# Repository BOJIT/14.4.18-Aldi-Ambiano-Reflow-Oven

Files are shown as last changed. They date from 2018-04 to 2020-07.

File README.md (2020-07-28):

# Aldi Ambiano Reflow Oven
Dirt cheap, easily replicable SMD reflow oven based on an Arduino Nano
and the £19.99 Aldi Ambiano Mini Oven

Developers: James Bennion-Pedley

Firmware closely based on work by https://github.com/giacu92/Arduino-Reflow-Oven-Controller

Project Write-Up Here: [https://bojit.dev/projects/Reflow_Oven/]

BOJIT Development Team

GPLv3 License

Copyright (c) 2018 BOJIT

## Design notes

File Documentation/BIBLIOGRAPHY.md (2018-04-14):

# Aldi Ambiano Reflow Oven
Dirt cheap, easily replicable SMD reflow oven based on an Arduino Nano
and the £19.99 Aldi Ambiano Mini Oven

Developers: James Bennion-Pedley

BOJIT Development Team

Sources and Links:

https://github.com/giacu92/Arduino-Reflow-Oven-Controller
https://github.com/0xPIT/reflowOvenController

MIT License

Copyright (c) 2018 BOJIT

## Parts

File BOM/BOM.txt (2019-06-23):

Ceramic Insulation	£14.00	https://www.ebay.co.uk/itm/CERAMIC-INSULATION-BLANKET-WOOD-BURNING-PIZZA-OVEN-FURNACE-WOOL-25mm-HIGH-TEMP/323415218165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
High-Temperature Wire	£1.79	https://www.ebay.co.uk/itm/High-Temperature-Oven-Heat-Fire-Resistant-Braided-Glass-Fibre-Wire-cable-2-5mm/112352955954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
Silicon Sealant		£2.79	https://www.ebay.co.uk/itm/BLACK-HIGH-TEMPERATURE-300-C-SILICONE-Heat-Resistant-ADHESIVE-SEALANT-Technicqll-/291793420033
2 x SSR			£6.34	https://www.ebay.co.uk/itm/2PCS-Solid-State-Relay-SSR-25DA-25A-250V-3-32V-DC-Input-24-380VAC-Output-NEW/141676282282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
Thermocouple + Breakout	£2.82	https://www.ebay.co.uk/itm/MAX6675-Module-K-Type-Thermocouple-Temperature-Sensor-For-Arduino-UK/153327741272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
16x2 LCD		£3.24	https://www.ebay.co.uk/itm/1602-16x2-LCD-Display-Module-BLUE-white-character-Serial-Arduino-Raspberry-PI/292453360759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

Total			£30.98

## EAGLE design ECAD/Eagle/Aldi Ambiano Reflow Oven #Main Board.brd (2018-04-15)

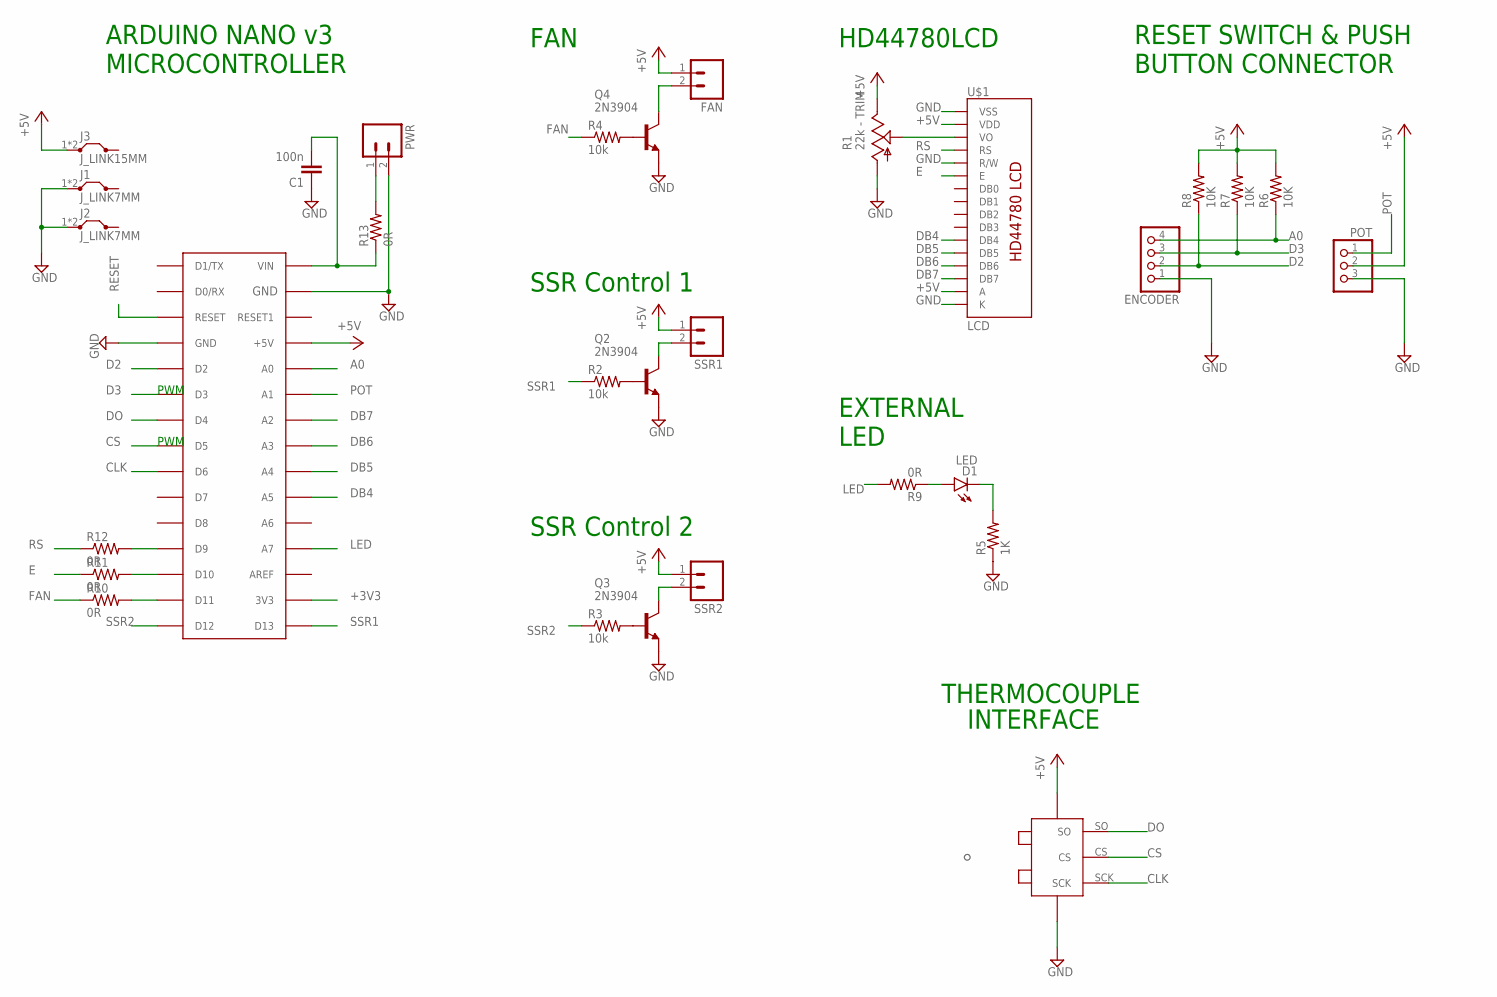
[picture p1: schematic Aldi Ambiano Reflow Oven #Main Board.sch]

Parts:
ARDUINO: Arduino Nano v3.0; PDIP-32
C1: 100n; CAP-PTH-5MM
D1: LED; LED3MM
ENCODER: PINHD-1X4/90; 1X04/90
FAN: M025MM; SCREWTERMINAL-5MM-2
J1, J2: J_LINK7MM; 07
J3: J_LINK15MM; 15
POT: PINHD-1X3/90; 1X03/90
PWR: M025MM; SCREWTERMINAL-5MM-2
Q2, Q3, Q4: 2N3904; TO92
R1: 22k - TRIM; CA9V
R2, R3, R4: 10k; R0207/3
R5: 1K; R0207/3
R6, R8: 10K; R0207/4
R7: 10K; R0207/3
R9: 0R; R0207/4
R10, R12: 0R; R0207/3
R11: 0R; R0207/6
R13: 0R; R0207/5
SSR1, SSR2: M025MM; SCREWTERMINAL-5MM-2
U$1: LCD; LCD-16X2-4HOLES
U$2: MAX6675_BREAKOUT

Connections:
+3V3: ARDUINO.3V3
+5V: ARDUINO.+5V, FAN.1, J3.1, J3.2, POT.2, R1.E, R6.2, R7.2, R8.2, SSR1.1, SSR2.1, U$1.2 (VDD), U$1.15 (A), U$2.VCC
A0: ARDUINO.A0, ENCODER.4, R6.1
CLK: ARDUINO.D6, U$2.SCK
CS: ARDUINO.D5, U$2.CS
D2: ARDUINO.D2, ENCODER.2, R8.1
D3: ARDUINO.D3, ENCODER.3, R7.1
DB4: ARDUINO.A5, U$1.11 (DB4)
DB5: ARDUINO.A4, U$1.12 (DB5)
DB6: ARDUINO.A3, U$1.13 (DB6)
DB7: ARDUINO.A2, U$1.14 (DB7)
DO: ARDUINO.D4, U$2.SO
E: R11.1, U$1.6 (E)
EINT: ARDUINO.D10, R11.2
FAN: R4.1, R10.1
FANJOINT: ARDUINO.D11, R10.2
GND: ARDUINO.GND, ARDUINO.GND1 (GND), C1.1, ENCODER.1, J1.1, J1.2, J2.1, J2.2, POT.3, PWR.2, Q2.3 (E), Q3.3 (E), Q4.3 (E), R1.A, R5.1, U$1.1 (VSS), U$1.5 (R/W), U$1.16 (K), U$2.GND
LED: ARDUINO.A7, R9.2
LEDINT: D1.A, R9.1
unnamed: PWR.1, R13.2
unnamed: Q2.1 (C), SSR1.2
unnamed: Q2.2 (B), R2.2
unnamed: R1.S, U$1.3 (VO)
unnamed: D1.K (C), R5.2
unnamed: Q3.1 (C), SSR2.2
unnamed: Q3.2 (B), R3.2
unnamed: FAN.2, Q4.1 (C)
unnamed: Q4.2 (B), R4.2
POT: ARDUINO.A1, POT.1
RESET: ARDUINO.RESET
RS: R12.1, U$1.4 (RS)
RSINT: ARDUINO.D9, R12.2
SSR1: ARDUINO.D13, R2.1
SSR2: ARDUINO.D12, R3.1
VIN: ARDUINO.VIN, C1.2, R13.1

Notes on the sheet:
SSR Control 1
THERMOCOUPLE
INTERFACE
ARDUINO NANO v3 MICROCONTROLLER
HD44780LCD
EXTERNAL LED
RESET SWITCH & PUSH BUTTON CONNECTOR
PWM
SSR Control 2
FAN

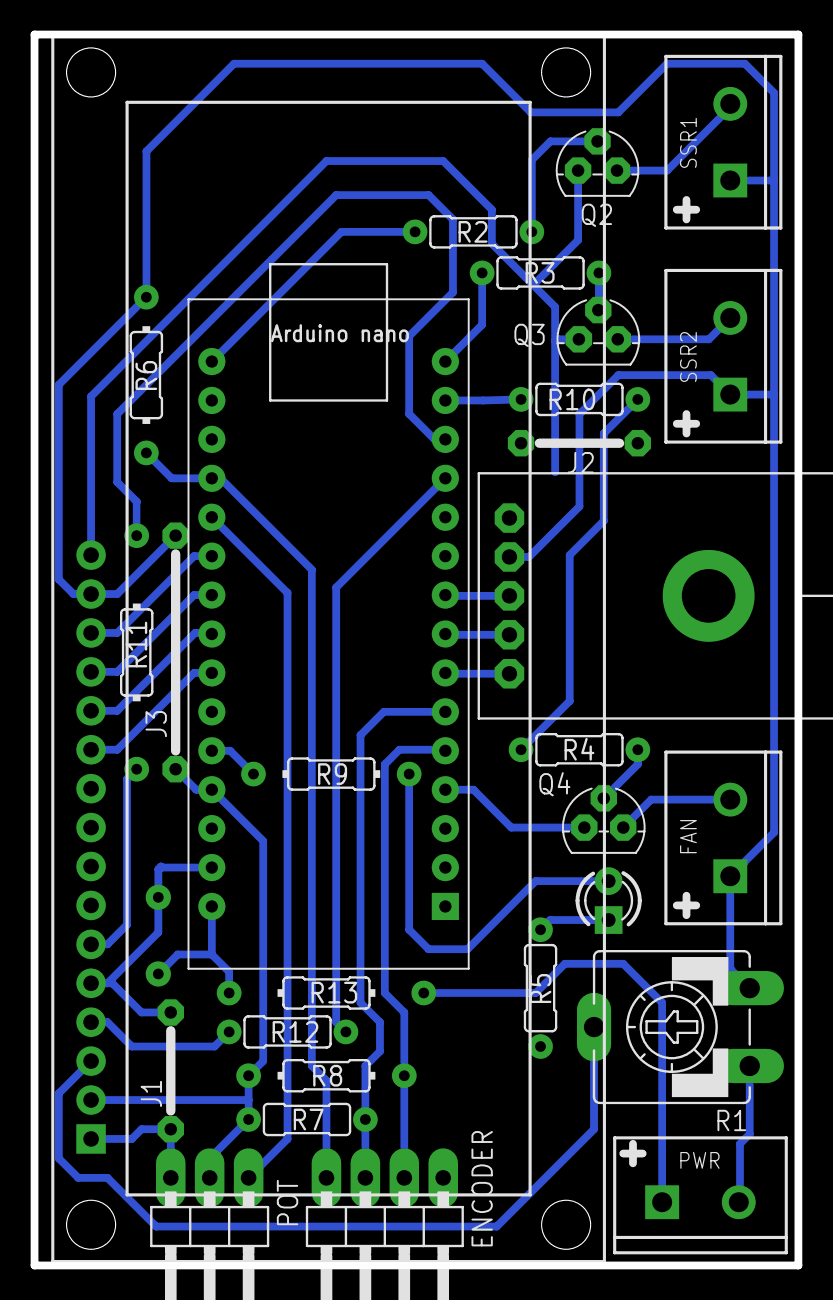
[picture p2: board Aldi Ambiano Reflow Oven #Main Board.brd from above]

Board: 2 copper layers, 49.8 x 80.3 mm, 30 parts (1 on the bottom side), 33 nets.

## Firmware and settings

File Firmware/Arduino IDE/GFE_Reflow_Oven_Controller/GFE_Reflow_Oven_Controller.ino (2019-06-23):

/*
   Revision  Description
   ========  ===========
   1.1       Arduino Nano v3 for GFE Hand Made Reflow Oven Controller board v1.1
             - Compiled for Arduino Nano.
             - Display changed to 16x2 Hitachi HD44780 Compatible.
             - added data output to diplay temperature vs time.
             - added possibility to choose between lead free of leaded solder paste profiles.
   
   1.2       Arduino Nano v3 for GFE Hand Made Reflow Oven Controller board v1.2
             - Added sounds.
             - Added temperature self check. The process self stops if unable to drive the oven.

   1.3       BOJIT modifications:
             - Interface is now in form of potentiometer and a rotary encoder
             - Simplified ECAD layout to use commonly available modules and a single-sided layout

   Temperature (Degree Celcius)                 Magic Happens Here!
   245-|                                               x  x
       |                                            x        x
       |                                         x              x
       |                                      x                    x
   200-|                                   x                          x
       |                              x    |                          |   x
       |                         x         |                          |       x
       |                    x              |                          |
   150-|               x                   |                          |
       |             x |                   |                          |
       |           x   |                   |                          |
       |         x     |                   |                          |
       |       x       |                   |                          |
       |     x         |                   |                          |
       |   x           |                   |                          |
   30 -| x             |                   |                          |
       |<  60 - 90 s  >|<    90 - 120 s   >|<       90 - 120 s       >|
       | Preheat Stage |   Soaking Stage   |       Reflow Stage       | Cool
    0  |_ _ _ _ _ _ _ _|_ _ _ _ _ _ _ _ _ _|_ _ _ _ _ _ _ _ _ _ _ _ _ _ _ _ _ _
                                                                  Time (Seconds)
*/

// ***** INCLUDES *****
#include <SPI.h>
#include <LiquidCrystal.h>
#include "Adafruit_MAX31855.h"
#include <PID_v1.h>
#include <PID_AutoTune_v0.h>

//#define USE_LCD_KEYPAD_SHIELD

// ***** CONSTANTS *****
#define TEMPERATURE_ROOM 50

#define TEMPERATURE_COOL_MIN 100
#define SENSOR_SAMPLING_TIME 1000
#define SOAK_TEMPERATURE_STEP 2
#define SOAK_MICRO_PERIOD 5000
#define DEBOUNCE_PERIOD_MIN 50

// ***** PID PARAMETERS *****
// Pre-Heating:
#define PID_KP_PREHEAT 60    //100
#define PID_KI_PREHEAT 0.05    //0.025
#define PID_KD_PREHEAT 20    //20
// Soaking:
#define PID_KP_SOAK 100  //300
#define PID_KI_SOAK 0.05       //0.05
#define PID_KD_SOAK 100          //250
// Reflowing:
#define PID_KP_REFLOW  300     //300
#define PID_KI_REFLOW  0.10    //0.05
#define PID_KD_REFLOW  350    //350

// Sample time:
#define PID_SAMPLE_TIME 1000

// Notes:
#define  note_c     261 //Hz
#define  note_cd    277 //Hz
#define  note_d     294 //Hz
#define  note_e     330 //Hz
#define  note_f     349 //Hz
#define  note_fg    370 //Hz
#define  note_g     392 //Hz
#define  note_ga    415 //Hz
#define  note_a     440 //Hz
#define  note_ab    466 //Hz
#define  note_b     494 //Hz
#define  note_C     523 //Hz

// ***** TYPE DEFINITIONS *****
typedef enum REFLOW_STATE
{
  REFLOW_STATE_IDLE,
  REFLOW_STATE_PREHEAT,
  REFLOW_STATE_SOAK,
  REFLOW_STATE_REFLOW,
  REFLOW_STATE_COOL,
  REFLOW_STATE_COMPLETE,
  REFLOW_STATE_TOO_HOT,
  REFLOW_STATE_ERROR,
  REFLOW_STATE_TUNING_PH
}
reflowState_t;

typedef enum REFLOW_STATUS
{
  REFLOW_STATUS_OFF,
  REFLOW_STATUS_ON
}
reflowStatus_t;

// ***** LCD MESSAGES *****
const char* lcdMessagesReflowStatus[] = {
  "Ready",
  "Preheat",
  "Soak",
  "Reflow",
  "Cool",
  "Complete",
  "Wait,hot",
  "Error",
  "Tuning"
};

// ***** DEGREE SYMBOL FOR LCD *****
unsigned char degree[8]  = { 140, 146, 146, 140, 128, 128, 128, 128 };

// ***** PIN ASSIGNMENT *****
#ifdef USE_LCD_KEYPAD_SHIELD
  #define btnRIGHT  0
  #define btnUP     1
  #define btnDOWN   2
  #define btnLEFT   3
  #define btnSELECT 4
  #define btnNONE   5
  #define ssrPin             2//6
  #define thermocoupleSOPin  11//5
  #define thermocoupleCSPin  12//4
  #define thermocoupleCLKPin 13//3
  #define lcdRsPin           8//9
  #define lcdEPin            9//10
  #define lcdD4Pin           4//A5
  #define lcdD5Pin           5//A4
  #define lcdD6Pin           6//A3
  #define lcdD7Pin           7//A2
  #define ledRedPin          A1//8
  #define buzzerPin          A2//7
  #define switchPin          A0
  #define lcdBrightnessPin   10
#else
  #define ssrPin             6
  #define thermocoupleSOPin  5
  #define thermocoupleCSPin  4
  #define thermocoupleCLKPin 3
  #define lcdRsPin           9
  #define lcdEPin            10
  #define lcdD4Pin           A5
  #define lcdD5Pin           A4
  #define lcdD6Pin           A3
  #define lcdD7Pin           A2
  #define ledRedPin          8
  #define buzzerPin          7
  #define switchPin          A0
#endif
int data = 0;

// ***** PID CONTROL VARIABLES *****
double setpoint;
double input;
double output;
double kp = PID_KP_PREHEAT;
double ki = PID_KI_PREHEAT;
double kd = PID_KD_PREHEAT;
const int windowSize = 2000;
unsigned long windowStartTime;
unsigned long nextCheck;
unsigned long nextRead;
unsigned long timerSoak;
unsigned long buzzerPeriod;

// ***** PID AUTOTUNE VARIABLES *****
byte ATuneModeRemember=2;
#define aTuneStep        1000
#define aTuneNoise       1
#define aTuneStartValue 1000;
unsigned int aTuneLookBack = 2;

// Reflow oven controller state machine state variable
reflowState_t reflowState;
// Reflow oven controller status
reflowStatus_t reflowStatus;
// Switch debounce timer
long lastDebounceTime;
// Seconds timer
long timerSeconds = 0;
long timeToCheck  = 20;
int checkTemperature = 0;

bool endOfPrevProcess = false;

int TEMPERATURE_SOAK_MIN = 0;
int TEMPERATURE_SOAK_MAX = 0;
int TEMPERATURE_REFLOW_MAX = 0;

String type = "";

// ***** DEFINING OBJECTS *****
// Specify PID control interface
PID reflowOvenPID(&input, &output, &setpoint, kp, ki, kd, DIRECT);
PID_ATune aTune(&input, &output);

// Specify LCD interface
LiquidCrystal lcd(lcdRsPin, lcdEPin, lcdD4Pin, lcdD5Pin, lcdD6Pin, lcdD7Pin);
Adafruit_MAX31855 thermocouple(thermocoupleCLKPin, thermocoupleCSPin, thermocoupleSOPin);

void setup()
{
  // SSR pin initialization to ensure reflow oven is off
  pinMode(ssrPin, OUTPUT);
  digitalWrite(ssrPin, LOW);

  // Buzzer pin initialization to ensure annoying buzzer is off
  digitalWrite(buzzerPin, LOW);
  pinMode(buzzerPin, OUTPUT);

  // LED pins initialization and turn on upon start-up (active low)
  pinMode(ledRedPin, OUTPUT);
  digitalWrite(ledRedPin, HIGH);

  // Tell the PID to range between 0 and the full window size
  reflowOvenPID.SetOutputLimits(0, windowSize);
  reflowOvenPID.SetSampleTime(PID_SAMPLE_TIME);

  // Start-up splash
  lcd.begin(16, 2);
  lcd.createChar(0, degree);
  lcd.clear();
  lcd.print("GFE Hand Made");
  lcd.setCursor(0, 1);
  lcd.print("Reflow Oven 1.2");

  // Serial communication at 57600 bps
  Serial.begin(57600);
  pinMode(13, OUTPUT);
  digitalWrite(13, LOW);

  // Turn off LED (active low)
  digitalWrite(ledRedPin, LOW);

  // Welcome sound
  soundStart();
  lcd.clear();

  // Initialize time keeping variable
  nextCheck = millis();
  // Initialize thermocouple reading variable
  nextRead = millis();
  reflowState = REFLOW_STATE_IDLE;

  #ifdef USE_LCD_KEYPAD_SHIELD
    pinMode(lcdBrightnessPin, OUTPUT);
    analogWrite(lcdBrightnessPin, 125);
  #endif
}

void loop()
{
  // Current time
  unsigned long now;

  // Time to read thermocouple?
  if (millis() > nextRead)
  {
    // Read thermocouple next sampling period
    nextRead += SENSOR_SAMPLING_TIME;
    // Read current temperature
    input = thermocouple.readCelsius();

    // If thermocouple problem detected
    if (isnan(input))
    {
      // Illegal operation
      reflowState = REFLOW_STATE_ERROR;
      reflowStatus = REFLOW_STATUS_OFF;
    }
  }

  if (millis() > nextCheck)
  {
    // Check input in the next seconds
    nextCheck += 1000;
    // If reflow process is on going
    if (reflowStatus == REFLOW_STATUS_ON)
    {
      // Toggle red LED as system heart beat
      digitalWrite(ledRedPin, !(digitalRead(ledRedPin)));
      // Increase seconds timer for reflow curve analysis
      timerSeconds++;
      
      // Send temperature and time stamp to serial as csv standard
      String dataToSend = "(" + (String)timerSeconds + "," + (String)setpoint + "," + (String)input + "," + (String)output + ")";
      char* buf = (char*) malloc(sizeof(char)*dataToSend.length()+1);

      dataToSend.toCharArray(buf, dataToSend.length()+1);
      Serial.println(buf);

      // Freeing the memory;
      free(buf);
    }
    else
    {
      // Turn off red LED
      digitalWrite(ledRedPin, HIGH);
    }

    // Clear LCD
    lcd.clear();
    lcd.setCursor(11, 1);
    if (reflowStatus == REFLOW_STATUS_ON)
    {
      lcd.print(type);
      // Print Stop Button
      lcd.setCursor(0, 1);
      lcd.print("stop");
      lcd.setCursor(6,1);
      lcd.print(timerSeconds);
      lcd.print(" s");
    }
    else
    {
      lcd.print("start");
      lcd.setCursor(0, 1);
      #ifdef USE_LCD_KEYPAD_SHIELD
        lcd.print("menu");
      #else
        lcd.print("prSet");
      #endif
    }

    // Print current system state
    lcd.setCursor(0, 0);
    lcd.print(lcdMessagesReflowStatus[reflowState]);
    // Move the cursor to the 2 line
    lcd.setCursor(9, 0);

    // If currently in error state
    if (reflowState == REFLOW_STATE_ERROR)
    {
      // No thermocouple wire connected
      lcd.print("TC Err");
    }
    else
    {
      // Print current temperature
      lcd.print(input);

      #if ARDUINO >= 100
        // Print degree Celsius symbol
        lcd.write((uint8_t)0);
      #else
        // Print degree Celsius symbol
        lcd.print(0, BYTE);
      #endif
      lcd.print("C ");
    }
  }

  // Reflow oven controller state machine
  switch (reflowState)
  {
    case REFLOW_STATE_IDLE:
      // If oven temperature is still above room temperature
      if (input >= TEMPERATURE_ROOM)
      {
        reflowState = REFLOW_STATE_TOO_HOT;
      }

      else
      {
        // If switch is pressed to start reflow process
        if (Serial.available() > 0)
        {
          //Leggo la stringa in arrivo dalla seriale.
          char dataIn[100] = {""};
          Serial.readBytes(dataIn, 100);
          String receivedString(dataIn);
          data = dataIn[0];
          //Serial.println("1 dataIn[0] = " + data);

          int iniPac = receivedString.indexOf('(');
          int endPac = receivedString.indexOf(')');

          //se ci sono i caratteri di inizio e fine pacchetto è un messaggio,
          //altrimenti ho ricevuto solo un dato da inserire in data.
          if (iniPac != -1 && endPac != -1 && endPac - iniPac > 1)
          {
            String packetIn = receivedString;
            packetIn = packetIn.substring(iniPac+1, endPac); //tolgo le parentesi

            int valoriIn[3] = {-100};
            for (int i=0; packetIn.indexOf(',') != -1; i++)
            {
              int index = packetIn.indexOf(',');
              valoriIn[i] = packetIn.substring(0, index).toInt();
              packetIn = packetIn.substring(index+1, packetIn.length());
            }

            TEMPERATURE_SOAK_MIN =    valoriIn[0];
            TEMPERATURE_SOAK_MAX =    valoriIn[1];
            TEMPERATURE_REFLOW_MAX =  valoriIn[2];

            type = " [C]";
            sendProfile();
          }

          else
          {
            data = dataIn[0];
            //Serial.println("2 dataIn[0] = " + data);
          }
        }
        
        if (analogRead(switchPin) < 30 || data == 10)
        {
          data = 0;
          #ifdef USE_LCD_KEYPAD_SHIELD
            delay(200);
          #endif

          if(TEMPERATURE_SOAK_MIN < 50)
            profileSet();
            
          //Saving data for heating check:
          checkTemperature = thermocouple.readCelsius();
          timeToCheck = 20;
          // Inizio il ciclo, mando i miei dati via seriale per settare il grafico.
          sendProfile();

          // Ora mando l'header per il file CSV
          Serial.println("Time Setpoint Input Output");
          // Intialize seconds timer for serial debug information
          nextCheck = millis();
          timerSeconds = 0;
          // Initialize PID control window starting time
          windowStartTime = millis();
          // Ramp up to minimum soaking temperature
          setpoint = TEMPERATURE_SOAK_MIN;
          // Turn the PID on
          reflowOvenPID.SetMode(AUTOMATIC);
          // Proceed to preheat stage
          reflowOvenPID.SetTunings(PID_KP_PREHEAT, PID_KI_PREHEAT, PID_KD_PREHEAT);
          reflowState = REFLOW_STATE_PREHEAT;
        }
        else if (data == 35) //tuning preheat code = # -> ASCII: 35
        {
          data = 0;
          lcd.clear();
          lcd.setCursor(0,0);
          lcd.print("TUNING PREHEAT");
          // Intialize seconds timer for serial debug information
          timerSeconds = 0;
          // Initialize PID control window starting time
          windowStartTime = millis();
          setpoint = 100;
          reflowOvenPID.SetMode(AUTOMATIC);
          reflowOvenPID.SetTunings(PID_KP_PREHEAT, PID_KI_PREHEAT, PID_KD_PREHEAT);

          //Setting autotuner:
          output=aTuneStartValue;
          aTune.SetNoiseBand(aTuneNoise);
          aTune.SetOutputStep(aTuneStep);
          aTune.SetLookbackSec((int)aTuneLookBack);
          AutoTuneHelper(true);
          type = " [PH]";

          //Going to autotuner mode:
          reflowState = REFLOW_STATE_TUNING_PH;
        }
      }
      break;

    case REFLOW_STATE_PREHEAT:
      reflowStatus = REFLOW_STATUS_ON;
      // If minimum soak temperature is achieve
      if (input >= TEMPERATURE_SOAK_MIN)
      {
        // Chop soaking period into smaller sub-period
        timerSoak = millis() + SOAK_MICRO_PERIOD;
        // Set less agressive PID parameters for soaking ramp
        reflowOvenPID.SetTunings(PID_KP_SOAK, PID_KI_SOAK, PID_KD_SOAK);
        // Ramp up to first section of soaking temperature
        setpoint = TEMPERATURE_SOAK_MIN + SOAK_TEMPERATURE_STEP;
        // Proceed to soaking state
        reflowState = REFLOW_STATE_SOAK;
      }
      break;

    case REFLOW_STATE_SOAK:
      // If micro soak temperature is achieved
      if (millis() > timerSoak)
      {
        timerSoak = millis() + SOAK_MICRO_PERIOD;
        // Increment micro setpoint
        setpoint += SOAK_TEMPERATURE_STEP;
        if (setpoint > TEMPERATURE_SOAK_MAX)
        {
          // Set agressive PID parameters for reflow ramp
          reflowOvenPID.SetTunings(PID_KP_REFLOW, PID_KI_REFLOW, PID_KD_REFLOW);
          // Ramp up to first section of soaking temperature
          setpoint = TEMPERATURE_REFLOW_MAX;
          // Proceed to reflowing state
          reflowState = REFLOW_STATE_REFLOW;
        }
      }
      break;

    case REFLOW_STATE_REFLOW:
      // We need to avoid hovering at peak temperature for too long
      // Crude method that works like a charm and safe for the components
      if (input >= (TEMPERATURE_REFLOW_MAX - 5))
      {
        // Set PID parameters for cooling ramp
        reflowOvenPID.SetTunings(PID_KP_PREHEAT, PID_KI_PREHEAT, PID_KD_PREHEAT);
        // Ramp down to minimum cooling temperature
        setpoint = TEMPERATURE_COOL_MIN;
        // Proceed to cooling state
        reflowState = REFLOW_STATE_COOL;
      }

      break;

    case REFLOW_STATE_COOL:
      // If minimum cool temperature is achieve
      if (input <= TEMPERATURE_COOL_MIN)
      {
        // Turn off reflow process
        reflowStatus = REFLOW_STATUS_OFF;
        // Proceed to reflow Completion state
        reflowState = REFLOW_STATE_COMPLETE;
        endOfPrevProcess = true;
        Serial.print("eof");
      }
      break;

    case REFLOW_STATE_COMPLETE:
      // Process ended. Display time and sound song.
      lcd.clear();
      lcd.print("REFLOW DONE!");
      lcd.setCursor(0,1);
      lcd.print("time: ");
      lcd.setCursor(11,1);
      lcd.print(timerSeconds);
      lcd.print(" s");
      soundComplete();
      
      // Reflow process ended
      reflowState = REFLOW_STATE_IDLE;
    break;

    case REFLOW_STATE_TOO_HOT:
      // If oven temperature drops below room temperature
      if (input < TEMPERATURE_ROOM)
      {
        // Ready to reflow
        reflowState = REFLOW_STATE_IDLE;
      }
      break;

    case REFLOW_STATE_ERROR:
      // If thermocouple problem is still present

      if (isnan(input))
      {
        // Wait until thermocouple wire is connected
        reflowState = REFLOW_STATE_ERROR;
      }
      else
      {
        // Clear to perform reflow process
        reflowState = REFLOW_STATE_IDLE;
      }
      break;

   case REFLOW_STATE_TUNING_PH:
      reflowStatus = REFLOW_STATUS_ON;

      if(timerSeconds > 180)
      {
        reflowStatus = REFLOW_STATUS_OFF;
        reflowState  = REFLOW_STATE_IDLE;
        lcd.clear();
        lcd.print("ERROR, aborting");
        soundError();
      }
      
      byte val = (aTune.Runtime());
      if (val!=0)
      {
        kp = aTune.GetKp();
        ki = aTune.GetKi();
        kd = aTune.GetKd();
        reflowOvenPID.SetTunings(kp,ki,kd);

        //Turn off autotune
        aTune.Cancel();
        AutoTuneHelper(false);

        //Going to IDLE:
        reflowStatus = REFLOW_STATUS_OFF;
        reflowState = REFLOW_STATE_IDLE;

        lcd.clear();
        lcd.print("DONE");
        lcd.print(" ");
        lcd.print(kp);
        lcd.setCursor(0,1);
        lcd.print(ki);
        delay(1000);
      }
   break;
  }

  // If switch 1 is pressed
  if (Serial.available() > 0) data = Serial.read();
  if (analogRead(switchPin) > 400 && analogRead(switchPin) < 800 || data == 100)
  {
    #ifdef USE_LCD_KEYPAD_SHIELD
      delay(200);
    #endif
    data = 0;
    // If currently reflow process is on going
    if (reflowStatus == REFLOW_STATUS_ON)
    {
      // Button press is for cancelling
      // Turn off reflow process
      reflowStatus = REFLOW_STATUS_OFF;
      // Reinitialize state machine
      reflowState = REFLOW_STATE_IDLE;
    }
    else
      #ifdef USE_LCD_KEYPAD_SHIELD
        delay(200);
        menu_page();
     #else
        profileSet();
     #endif
  }
  else if (data == 36)
  {
    // Turn off reflow process
    reflowStatus = REFLOW_STATUS_OFF;
    // Reinitialize state machine
    reflowState = REFLOW_STATE_IDLE;
  }

  // PID computation and SSR control
  if (reflowStatus == REFLOW_STATUS_ON)
  {
    if (reflowState == REFLOW_STATE_PREHEAT && timeToCheck <= timerSeconds)  //check for SSR failures on PREHEAT stage
    {
      if (input < checkTemperature)
      {
        reflowStatus = REFLOW_STATUS_OFF;
        reflowState = REFLOW_STATE_IDLE;
        lcd.clear();
        lcd.print("ERROR  check");
        lcd.setCursor(0,1);
        lcd.print("Power or SSR");
        soundError();
      }
      
      timeToCheck = timerSeconds+20;
      checkTemperature = input;
    }
    
    now = millis();

    if(reflowState != REFLOW_STATE_TUNING_PH)
      reflowOvenPID.Compute();

    if ((now - windowStartTime) > windowSize)
    {
      // Time to shift the Relay Window
      windowStartTime += windowSize;
    }
    if (output > (now - windowStartTime))
    {
      //Serial.println("ssrPin, HIGH");
      digitalWrite(ssrPin, HIGH);
    }
    else
    {
      digitalWrite(ssrPin, LOW);
      //Serial.println("ssrPin, LOW");
    }
  }
  // Reflow oven process is off, ensure oven is off
  else
  {
    digitalWrite(ssrPin, LOW);
    lcd.setCursor(7, 1);
    lcd.print(" ");
  }
}

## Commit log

2018-04-15 Pad Clearance Changed
    [Aldi Ambiano Reflow Oven #Main Board.brd]
2019-06-23 addd BOM

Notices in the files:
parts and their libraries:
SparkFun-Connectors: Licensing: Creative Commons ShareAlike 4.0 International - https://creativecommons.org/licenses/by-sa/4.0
